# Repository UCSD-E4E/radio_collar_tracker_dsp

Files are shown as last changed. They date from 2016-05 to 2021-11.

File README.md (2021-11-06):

radio_collar_tracker_drone
====================
Airborne Wildlife Radio Collar Tracker - UAS Component

Engineers for Exploration, UCSD Project

Installing the payload software
===============================
1.	Install the required dependencies
	1.	python3
		1.	`apt-get install python3`
	2.  boost
		1.	`apt-get install libboost-all-dev`
	3.  pythom-mako
		1.	`apt-get install python-mako`
	4.  six
		1.	`pip install six`
	5.  requests
		1.	`pip install requests`
	7.  enum
		1.	`pip install enum`
	8.  pyserial
		1.  `pip3 install pyserial`
	5.	libusb-dev
		1.	`apt-get install libusb-1.0-0-dev`
	9.	libuhd 3.11.01
		1.	`apt-get install cmake build-essential`
		2.	`git clone git://github.com/EttusResearch/uhd.git`
		3.	`cd <uhd_repo>/host`
		4.	`git checkout v3.11.0.1`
		5.	`mkdir build`
		6.	`cd build`
		7.	`cmake -DENABLE_B100=OFF -DENABLE_X300=OFF -DENABLE_N230=OFF -DENABLE_USRP1=OFF -DENABLE_USRP2=OFF -DENABLE_OCTOCLOCK=OFF -DENABLE_RFNOC=OFF -DENABLE_MPMD=OFF -DENABLE_EXAMPLES=OFF -DENABLE_MANUAL=OFF -DENABLE_TESTS=OFF ../`
		8.	`make`
		9.	`make install`
		10.	`ldconfig`
		11.	`/usr/local/lib/uhd/utils/uhd_images_downloader.py -t b2xx*`
	10.	fftw
		1.	`wget http://www.fftw.org/fftw-3.3.8.tar.gz`
		2.	`tar -xzf fftw-3.3.8.targ.gz`
		3.	`cd <fftw>`
		4.	`./bootstrap.sh && ./configure --enable-threads 
		--enable-generic-simd128 --enable-generic-simd256`
		5.	`make`
		6.	`make install`
2.	Install the software
	1.	`cd <radio_collar_tracker_drone>`
	2.	`git checkout online_proc`
	2.  `./autogen.sh`
	3.  `./configure`
	4.	`make`
	5.	`sudo make install`

tl;dr
-----
1.	`sudo apt-get update`
2.	`sudo apt-get install -y git vim htop gdb valgrind cmake build-essential python3 libboost-all-dev python-mako python3-pip libusb-1.0-0-dev autoconf pkg-config picocom python-pip zip wget tmux`
3.	`sudo pip2 install six requests`
4.	`sudo pip3 install pyserial`
5.	`git clone git://github.com/EttusResearch/uhd.git`
6.	`cd uhd/host`
7.	`git checkout v3.11.0.1`
8.	`mkdir build`
9.	`cd build`
10.	`cmake -DENABLE_B100=OFF -DENABLE_X300=OFF -DENABLE_N230=OFF -DENABLE_USRP1=OFF -DENABLE_USRP2=OFF -DENABLE_OCTOCLOCK=OFF -DENABLE_RFNOC=OFF -DENABLE_MPMD=OFF -DENABLE_EXAMPLES=OFF -DENABLE_MANUAL=OFF -DENABLE_TESTS=OFF ../`
11.	`make -j8`
12.	`sudo make install`
13.	`sudo ldconfig`
14.	`sudo /usr/local/lib/uhd/utils/uhd_images_downloader.py -t b2xx*`
15.	`cd ../../..`
16.	`wget http://www.fftw.org/fftw-3.3.8.tar.gz`
17.	`tar -xzf fftw-3.3.8.tar.gz`
18.	`cd fftw-3.3.8`
19.	`./bootstrap.sh`
20.	`./configure --enable-threads --enable-generic-simd128 --enable-generic-simd256`
21.	`make -j8`
22.	`sudo make install`
23.	`cd ../`
24.	`git clone git://github.com/UCSD-E4E/radio_collar_tracker_dsp.git`
25.	`cd radio_collar_tracker_dsp`
26.	`git checkout master`
27.	`./autogen.sh`
28.	`./configure`
29.	`make -j8`
30.	`sudo make install`

Running the payload software (standalone)
=========================================
`sudo service rctrun start`

# Running the payload software (hardware-based initialization)

## Payload Power On Procedure
1.	Disconnect power to AUTOPILOT, PAYLOD
2.	Connect power to PAYLOAD
3.	Connect power to AUTOPILOT
4.	Flip PAYLOAD SWITCH to the ON position.
5.	Wait for the PAYLOAD STATUS LIGHT to turn green for at least 10 seconds.
6.	Flip PAYLOAD SWITCH to the OFF position.
7.	Wait for the PAYLOAD STATUS LIGHT to turn off within 5 seconds.
8.	Connect the GROUND CONTROL STATION to the AUTOPILOT.
9.	Payload Power On Procedure complete.

## Payload Start Procedure
1.	Complete the Payload Power On Procedure.
2.	Flip PAYLOAD SWITCH to the ON position.
3.	Wait for the PAYLOAD STATUS LIGHT to turn green for at least 10 seconds.
4.	Payload Start Procedure complete.

## Payload Stop Procedure
1.	Flip PAYLOAD SWITCH to the OFF position.
2.	Wait for the PAYLOAD STATUS LIGHT to turn off within 5 seconds.
3.	Payload Stop Procedure complete.

## Payload Power Off Procedure
1.	Complete the Payload Stop Procedure.
2.	Disconnect power to the PAYLOAD.
3.	Payload Power Off Procedure complete.

Output Data Format
==================
Output data location is specified in `/usr/local/etc/rct_config`.  Each run
consists of a number of IQ (raw) data files, GPS data files, and a metadata
file.  The name format for each type of file is `[type]_[run]_[file_num]`.  
The `type` field specifies, in capital letters, the type of file (i.e. RAW_DATA,
GPS, or META).  The `run` field specifies a numerical identifier for each run,
assigned sequentially. This field is always 6 characters wide, zero padded.  The
`file_num` field specifies the ordering of the IQ data files.  The first file
recorded would have a file number of 1, sequential files having sequential
numbers.  This field is always 6 characters wide, zero padded.

The raw data files contain the raw IQ data recorded as pairs of 8-bit unsigned
integers.  Each pair represents the in-phase and quadrature components of the
recorded signal in sequence.  See
https://en.wikipedia.org/wiki/In-phase_and_quadrature_components for an
explanation of IQ signal representation.

The GPS data files contain timestamped snapshots of autopilot telemetry.

The metadata file contains metadata pertaining to the configuration of the
payload.  Each line contains one field.  The key for each field is followed by a
colon, then the value for that field, followed by a newline character:
```
[field_name]: [field_value]
```
The whitespace between the colon and field value is optional, and preferred for
readability, but cannot be a newline.  The metadata file contains the following
fields: local IQ data start time (UTC in seconds), SDR center frequency (Hz),
SDR sampling frequency (Hz), SDR gain (dB).

# Information for Developers
## Connecting to the payload
1.	Connect to the `ubnt` GROUND WIFI LINK.
2.	Look for the sticker with the device hostname on the payload.
3.	SSH in using `e4e@hostname.local`

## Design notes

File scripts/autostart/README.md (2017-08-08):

# Operation

The autostart module should accomplish the following:
* When the switch is moved to the "on" position, execute `rct_sdr_starter`.
* Monitor the state of `rct_sdr_starter` to ensure correct operation.
* When the switch is moved to the "off" position, send `SIGTERM` to `rct_sdr_starter`.
* Enable multiple runs without rebooting the system.

# Configuring autostart

If the file `/usr/local/etc/rct_autostart` exists, autostart will be enabled.

# Pinout:
5V0 -> J13-4

1V8 -> J13-10

GND -> J13-9

GPIO1 -> J13-11

GPIO2 -> J13-13

GPIO3 -> J13-15

GPIO4 -> J13-17

GPIO5 -> J13-19

SW1 -> J13-21

# Structure
`rctstart` is the Linux Standard Base init script that starts the `rctrun` service at boot.

`rctrun` is the state machine that manages initializing and starting all devices.

`rct_blink` is the LED mapping program that drives the LEDs.

## rctstart

`rctstart` is the init script that runs at boot.  At current, this only starts and stops the `rctrun` process.  It uses the `/var/lock/rctstart` lock to ensure that only one instance of `rctrun` exists.  The source for this is `rctstart.sh`

## rctrun

`rctrun` is the state machine that manages the initialization and starting of all devices and recording.  There are several state machines for each of the GPS, SDR, and output directory.  These initialize and sanity check the devices to ensure that the next run will operate properly.  `rctrun` will automatically launch and stop the necessary programs.

`rct_blink` is the program that drives the LEDs based on the state of `rctrun`.  State information is stored in `/var/local/rct.dat`.

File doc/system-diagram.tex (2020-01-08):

\documentclass[tikz, convert={outfile=\jobname.svg}]{standalone}
\usetikzlibrary{arrows, positioning, quotes, graphs, graphdrawing, fit, topaths}
\usegdlibrary{force}
\begin{document}
	\tikz [	node distance=1 cm, 
			env/.style={}, 
			block/.style={draw,rectangle},
			every edge quotes/.append style={font=\tiny, rectangle}]{
		\node (rf) [env] {Transmitter Signal (1)};
		
		\node (ant) [block, below=of rf] {Antenna (2)};
		\node (lna) [block, below=of ant] {Low Noise Amplifier (3)};
		\node (sdr) [block, below=of lna] {Software Defined Radio (4)};
		\node (ping_detect) [block, below=of sdr] {Ping Detector (5)};
		\node (sensor_fusion) [block, below=of ping_detect] {Sensor Fusion (6)};
		\node (sys_mgr) [block, left=of sensor_fusion] {System Manager (12)};
		\node (ui_board) [block, below=of sensor_fusion] {UI Board (11)};
		\node (pgps) [block, left=of ui_board] {Payload GPS (9)};
		\node (pcompass) [block, below=of ui_board] {Payload Compass (10)};
		\node (disk) [block, right=of sensor_fusion] {Disk (13)};
		\node (obc) [draw, label={[anchor=south west]north west:On-Board Computer (14)}, fit=(ping_detect) (sys_mgr) (sensor_fusion) (disk)] {};
		
		\node (dmag) [block, left=of ant] {Drone Compass (17)};
		\node (dgps) [block, left=of dmag] {Drone GPS (18)};
		\node (px4) [block, below=of dgps] {Flight Controller (19)};
		\node (esc) [block, below=of px4] {ESCs (22)};

		\node (drone)[draw, label={[anchor=south west]north west:Drone (15)}, fit=(obc) (sdr) (lna) (ant) (ui_board) (pgps) (pcompass) (dgps) (dmag) (px4)] {};
		
		\node (ping_est) [block, left=of drone] {Ping Estimator (7)};
		\node (ping_vis) [block, below=of ping_est] {Estimate Visualization (8)};
		\node (ctrl) [block, below=of ping_vis] {Payload Control (20)};
		\node (mp) [block, left=of px4] {Vehicle Control (21)};

		\draw (rf) edge[-stealth', "RF Signal"] (ant)
			  (ant) edge[-stealth', "RF Signal over Coax"] (lna)
			  (lna) edge[-stealth', "RF Signal over Coax"] (sdr)
			  (sdr) edge[-stealth', "IQ Data"] (ping_detect)
			  (ping_detect) edge[-stealth', "Detected Pings"] (sensor_fusion)
			  (ui_board) edge[-stealth', "Sensor Data"'] (sensor_fusion)
			  (sys_mgr) edge[-stealth', "System Status"'] (ui_board)
			  (pgps) edge[-stealth', "NMEA"] (ui_board)
		      (pcompass) edge[-stealth', "Pose"] (ui_board)
			  (sensor_fusion) edge[-stealth', "Pings"] (disk)
			  				  edge[-stealth', out=150, in=0, "Pings"] (ping_est)
			  (ping_est) edge[-stealth', "Estimates"] (ping_vis)
			  (px4) edge[stealth'-, "NMEA"] (dgps)
			  		edge[stealth'-, "Heading"] (dmag)
			  		edge[stealth'-stealth', "MAVLink"] (mp)
			  		edge[-stealth', "PWM"] (esc)
			  (ctrl) edge[-stealth', out=5, in=180, "Commands"] (sys_mgr)
			  		 edge[stealth'-, out=0, in=185, "System Status"'] (sys_mgr);
		\node (gcs) [block, label={[anchor=south west]north west:Ground Control Station (16)}, fit=(ping_est) (ping_vis) (mp) (ctrl)] {};
	}

\end{document}

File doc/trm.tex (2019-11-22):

\documentclass{report}
% \usepackage{draftwatermark}
\title{Radio Collar Tracker Technical Reference Manual}
\author{Nathan Hui, Project Lead\\Engineers for Exploration, UC San Diego}
\date{\today\\v0.3}
\usepackage{fullpage,bookmark,hyperref,listings,lmodern,siunitx}
\usepackage[toc,nonumberlist]{glossaries}
\makeglossaries
\hypersetup{
    colorlinks,
    citecolor=black,
    filecolor=black,
    linkcolor=black,
    urlcolor=blue
}
\renewcommand*{\chapterautorefname}{Chapter}
\lstset{
	basicstyle=\ttfamily,
	breaklines=true
}
\renewcommand*{\chapterautorefname}{Chapter}
\begin{document}
	\maketitle
	\tableofcontents
	\listoffigures
	\listoftables
	\lstlistoflistings
	\chapter{Overview}
	\chapter{Signal Processing}
		\section{Version 1}

	\chapter{Payload}
		\section{UP Core}
			\subsection{Locating the UP Core}
				The UP Core is currently configured to automatically connect to either the Sealab or UCSD-Protected networks.  It has a hostname of e4e-UPCORE-1.

				At current, the Sealab network is configured as a bridge to the UCSD network, so all devices can be accessed via hostname.dynamic.ucsd.edu.

				The UP Core can always be accessed (on UCSD campus) at e4e-upcore-1.dynamic.ucsd.edu.

				Due to this network configuration, the UP Core is accessible only via SSH public key authentication.  To add a public key, append the appropriate key to \lstinline[language=sh]{/home/e4e/.ssh/authorized_keys}.
		\section{UI Board} \label{sec:ui}
			\subsection{Flashing the UI Board} \label{ssec:flash_ui}
				The UI Board currently uses an Atmel ATmega32u4.  The best way to flash this is to use the Dragon ISP (In System Programmer) to load the program into flash.  The recommended way to interact with the Dragon ISP for Atmel microcontrollers is by using \lstinline[language=sh]{avrdude}.  See Listing \ref{lst:avrdude_usage} for details on specific command line options.

				For the UI Board, use the following options:

				\begin{itemize}
					\item \lstinline{partno}: \lstinline{m32u4}
					\item \lstinline{bitclock}: \lstinline{10}
					\item \lstinline{programmer}: \lstinline{dragon_isp}
					\item \lstinline{port}: \lstinline{usb}
					\item \lstinline{memtype}: \lstinline{flash}
				\end{itemize}
				
				For example, if we were to flash the file \lstinline{foo.hex} to the UI Board, we would use the command in Listing \ref{lst:avrdude_example}.

				\begin{lstlisting}[language=sh, caption={Example avrdude command}, label={lst:avrdude_example}]
avrdude -p m32u4 -c dragon_isp -B 10 -P usb -U flash:w:foo.hex
				\end{lstlisting}

				\begin{lstlisting}[caption={\lstinline{avrdude} usage}, label={lst:avrdude_usage}]
Usage: avrdude [options]
Options:
  -p <partno>                Required. Specify AVR device.
  -b <baudrate>              Override RS-232 baud rate.
  -B <bitclock>              Specify JTAG/STK500v2 bit clock period (us).
  -C <config-file>           Specify location of configuration file.
  -c <programmer>            Specify programmer type.
  -D                         Disable auto erase for flash memory
  -i <delay>                 ISP Clock Delay [in microseconds]
  -P <port>                  Specify connection port.
  -F                         Override invalid signature check.
  -e                         Perform a chip erase.
  -O                         Perform RC oscillator calibration (see 
                             AVR053). 
  -U <memtype>:r|w|v:<filename>[:format]
                             Memory operation specification.
                             Multiple -U options are allowed, each request
                             is performed in the order specified.
  -n                         Do not write anything to the device.
  -V                         Do not verify.
  -u                         Disable safemode, default when running from a
                             script.
  -s                         Silent safemode operation, will not ask you 
                             if fuses should be changed back.
  -t                         Enter terminal mode.
  -E <exitspec>[,<exitspec>] List programmer exit specifications.
  -x <extended_param>        Pass <extended_param> to programmer.
  -y                         Count # erase cycles in EEPROM.
  -Y <number>                Initialize erase cycle # in EEPROM.
  -v                         Verbose output. -v -v for more.
  -q                         Quell progress output. -q -q for less.
  -l logfile                 Use logfile rather than stderr for 
                             diagnostics.
  -?                         Display this usage.
				\end{lstlisting}

			\subsection{Compiling Programs for the UI Board} \label{ssec:ui_compile}
				\subsubsection{Arduino IDE} \label{sssec:ui_arduino_compile}
					To use the Arduino IDE to compile programs, load the code into the Arduino IDE.  In the IDE, set the \lstinline{Board} option to \lstinline{Arduino Leonardo}, and enable verbose output for compilation.

					Compile the code by clicking the \lstinline{Verify} button, or by selecting \lstinline{Verify/Compile} from the \lstinline{Sketch} menu.  In the output area, look for the line that invokes \lstinline{avr-objcopy} and outputs a file that hax the \lstinline{.hex} extension.  This is the file that needs to be uploaded to the UI Board using the instructions in Subsection \ref{ssec:flash_ui}.

				\subsubsection{avr-gcc} \label{sssec:ui_make_compile}
					If the Arduino IDE is not available, or not an option, we can use the AVR compilation toolchain.  This is a version of \lstinline{gcc} that compiles specifically to the AVR instruction set.

					In general, use \lstinline{avr-g++} or \lstinline{avr-gcc} to compile the individual object files as appropriate.  Then use \lstinline{avr-g++} to link all the object files and libraries into an \lstinline{.elf} (Executable and Linkable Format).  Finally, use \lstinline{avr-objcopy} to copy the text and data portions of the program into the appropriate locations in the \lstinline{.hex} file (Intel Hexcode).

					An example compilation may look like the following:

					\begin{lstlisting}[language=sh, caption={Example avr-gcc compilation}, label={lst:avr-gcc_example}]
avr-g++ -c test.cpp -o test.o
avr-g++ -o test.elf test.o
avr-objcopy -j .text -j .data -O ihex test.elf test.hex
					\end{lstlisting}

					See the \lstinline{ui_board} branch of the Radio Collar Tracker Github\footnote{\url{https://github.com/UCSD-E4E/radio_collar_tracker_drone/blob/ui_board/src/arduino/Makefile}} for a makefile containing the rules to compile, link, and format the program.
			\subsection{UI Board Functionality}\label{ssec:ui_functional}
				The UI Board shall gather data from the following sensors: GPS, compass, and user switch.  It must transmit the data and state information to the UP Core as specified in Section \ref{ssec:ui_obc_msg}.  Simultaneously, the UI Board shall also receive status messages from the UP Core as specified in Section \ref{ssec:obc_ui_msg}, and switch LEDs in the appropriate response.  See Tables \ref{tbl:led1_states}, \ref{tbl:led2_states}, \ref{tbl:led3_states}, and \ref{tbl:led4_states} for the state tables.

				\begin{table}[htp]
					\centering
					\caption{LED 1 (System) State Table}
					\label{tbl:led1_states}
					\begin{tabular}{c|c}
						System State & LED State \\ \hline
						Init & Blinking (5 Hz)\\
						Wait for Start & Off\\
						Wait for End & Blinking (1 Hz)\\
						Finish & Solid \\
						Fail & Off
					\end{tabular}
				\end{table}

				\begin{table}[htp]
					\centering
					\caption{LED 2 (Storage) State Table}
					\label{tbl:led2_states}
					\begin{tabular}{c|c}
						Storage State & LED State \\\hline
						Init & Blinking (5 Hz)\\
						Ready & Solid \\
						Fail & Off\\
						Retry & Blinking (1 Hz)
					\end{tabular}
				\end{table}			

				\begin{table}[htp]
					\centering
					\caption{LED 3 (SDR) State Table}
					\label{tbl:led3_states}
					\begin{tabular}{c|c}
						SDR State & LED State \\\hline
						Init & Blinking (5 Hz)\\
						Ready & Solid\\
						Fail & Off\\
						Retry & Blinking (1 Hz)
					\end{tabular}
				\end{table}

				\begin{table}[htp]
					\centering
					\caption{LED 4 (GPS) State Table}
					\label{tbl:led4_states}
					\begin{tabular}{c|c}
						GPS State & LED State \\\hline
						Init & Blinking (5 Hz)\\
						Ready & Solid\\
						Fail & Off\\
						Retry & Blinking (1 Hz)
					\end{tabular}
				\end{table}

				LED 5 shall be solid in and only in the following states: GPS is Ready, SDR is Ready, STR is Ready, and Sys is wait\_start.
		\section{UI Board to GPS/Compass Protocol Specification}\label{sec:ui_gps_mag_comm_spec}
			The GPS/Compass module is a DroTek Ublox GPS and Compass Module, configured with the XL patch antenna.
			\subsection{GPS}
				The GPS is a UBlox M8N.  This has a 5V TTL UART configured with 8N1 frames and 9600 baud.  Data is transmitted as a NMEA 0183 stream, with a nominal message rate of \SI{1}{\Hz}.
			\subsection{Compass}
				The compass is a Honeywell HMC5983 magnetometer\footnote{\url{https://aerocontent.honeywell.com/aero/common/documents/myaerospacecatalog-documents/Defense_Brochures-documents/HMC5983_3_Axis_Compass_IC.pdf}}.  This has an I2C bus, with an address of \lstinline{0x3C}.  Reference the datasheet for communication protocols.
		\section{UI Board to UP Core Protocol Specification}\label{sec:obc_uibrd_comm_spec}
			Data transmission shall take place as a software serial port over USB.  This connection shall go from the CN7 connector on the UP Core to the P2 connector on the UI Board.  This physical link shall comply with USB 2.0 standards.

			The virtual serial port shall be configured as 8N1 with a baud rate of 9600.

			Data shall be formatted as JSON dictionaries.

			\subsection{UP Core to UI Board}\label{ssec:obc_ui_msg}
				The UP Core shall transmit a status message at \SI{1}{\hertz} nominal frequency. This message shall be formatted as a JSON dictionary with the following keys: \lstinline{STR}, \lstinline{SDR}, \lstinline{SYS}.  See Listing \ref{lst:upcore_status_msg} for an example message.  See Table \ref{tbl:obc_status_vals} for the status values.  These keys are not guaranteed to come in any particular order.

				\begin{lstlisting}[caption={UP Core Status Message}, label={lst:upcore_status_msg}]
{"STR": 3, "SYS": 3, "SDR": 4}
				\end{lstlisting}

				\begin{table}[htp]
					\centering
					\caption{Status Message Lookup Tables}
					\label{tbl:obc_status_vals}
					\begin{tabular}{c|c|c}
						Storage State & State Name & STR value \\\hline
						Init & \lstinline!STR_INIT! & 0\\
						Ready & \lstinline!STR_READY! & 1\\
						Fail & \lstinline!STR_FAIL! & 2\\
						Retry & \lstinline!STR_RETRY! & 3
					\end{tabular}
					
					\begin{tabular}{c|c|c}
						SDR State & State Name & SDR value \\\hline
						Init & \lstinline!SDR_INIT! & 0\\
						Ready & \lstinline!SDR_READY! & 1\\
						Fail & \lstinline!SDR_FAIL! & 2\\
						Retry & \lstinline!SDR_RETRY! & 3
					\end{tabular}
					
					\begin{tabular}{c|c|c}
						GPS State & State Name & GPS value\\\hline
						Init & \lstinline!GPS_INIT! & 0\\
						Ready & \lstinline!GPS_READY! & 1\\
						Fail & \lstinline!GPS_FAIL! & 2\\
						Retry & \lstinline!GPS_RETRY! & 3
					\end{tabular}
					
					\begin{tabular}{c|c|c}
						System State & State Name & SYS value\\\hline
						Init & \lstinline!SYS_INIT! & 0\\
						Wait for Start & \lstinline!SYS_WAIT_FOR_START! & 1\\
						Wait for End & \lstinline!SYS_WAIT_FOR_END! & 2\\
						Finish & \lstinline!SYS_FINISH! & 3\\
						Fail & \lstinline!SYS_FAIL! & 4
					\end{tabular}
				\end{table}

				Each module may enter any state at any time.
			\subsection{UI Board to UP Core}\label{ssec:ui_obc_msg}
				The UI Board shall act as a data aggregator for the UP Core, collecting telemetry and state information from the GPS, compass, and user switch.  The UI Board shall then pass these data on to the UP Core as a JSON dictionary with the following keys: \lstinline{lat}, \lstinline{lon}, \lstinline{hdg}, \lstinline{tme}, \lstinline{run}, \lstinline{fix}, \lstinline{sat}.  These keys are not guaranteed to come in any particular order.  See Table \ref{tbl:ui_board_sensor_fields} for a description of the individual fields, and Listing \ref{lst:ui_board_sensor_msg} for an example message.

				\begin{lstlisting}[caption={UI Board Sensor Message}, label={lst:ui_board_sensor_msg}]
{"lat": 327054113, "hdg": 270, "lon": -1171710165, "tme": 1530025076, "run": true, "fix": 1, "sat": 14}
				\end{lstlisting}

				\begin{table}[htp]
					\centering
					\caption{Sensor Message Field Descriptions}
					\label{tbl:ui_board_sensor_fields}
					\begin{tabular}{c|c|c|c}
						Field & Key & Data Type & Description\\\hline
						GPS Latitude & \lstinline'lat' & int & GPS Latitude in WGS84 datum, formatted as lat $\times$ 1e7\\
						GPS Longitude & \lstinline'lon' & int & GPS Longitude in WGS84 datum, formatted as lon $\times$ 1e7\\
						Vehicle Heading & \lstinline'hdg' & int & Vehicle Heading in degree East of Magnetic North\\
						GPS Time & \lstinline'tme' & int & GPS Timestamp in seconds since GPS epoch (06 Jan 1980)\\
						User Switch & \lstinline'run' & bool & True if the switch is in the ON position, False otherwise\\
						GPS Fix Type & \lstinline'fix' & int & GPS Fix, Differential GPS Fix, RTK Fix\\% TODO Fix value assignments!
						GPS Satellite Count & \lstinline'sat' & int & Number of satellites used in current fix
					\end{tabular}
				\end{table}

				This sensor data shall be transmitted at a nominal rate of \SI{1}{\hertz}.
		\section{Payload Configuration}
			All configuration options are set in the file \lstinline[language=sh]{/usr/local/etc/rct_config}.  This file is owned by \lstinline[language=sh]{root}, and should have permissions set to \lstinline{644}.
			\subsection{Center Frequency}
				The center frequency for the SDR is set to CENTER\_FREQ by the line \lstinline[language=sh]{freq=CENTER_FREQ}.  This is the center frequency the SDR is recording at, in Hz.  Due to physical limitations of the SDR, set this to be at least 1 kHz away from the nearest frequency that needs to be measured.
			\subsection{Sampling Frequency}
				The sampling frequency for the SDR is set to SAMPLING\_FREQ by the line \lstinline[language=sh]{sampling_freq=SAMPLING_FREQ}.  This is the sampling frequency that the SDR is recording at, in samples per second.  Due to physical limitations of the SDR, this value can be only be set to between 200 kHz and 56 MHz in steps of 1 Hz.  Ensure that all frequencies to be recorded are within half the sampling frequency away from the center frequency.
			\subsection{RF Gain}
				The RF gain for the SDR receive chan is set to RF\_GAIN by the line \lstinline[language=sh]{gain="RF_GAIN"}.  This is the gain that is applied to the RF signal in the LNA stage in the SDR, in dB.  Due to physical limitations of the SDR, this value can only be set to between 0 dB and 76 dB, in steps of 1 dB.  Ensure that all recorded signals are not clipping with any new gain setting.  Ideally, the loudest signal should result in an amplitude no greater than 80\% of the dyanmic range of the SDR.
			\subsection{Initializing the USRP B200-mini(-i)}
				The USRP B200-mini and USRP B200-mini-i are not capable of retaining an FPGA image between boots.  This image needs to be flashed every boot.  This can be accomplished via command line.

				\begin{lstlisting}[language=sh]
sudo uhd_usrp_probe --args="type=b200" --init-only
				\end{lstlisting}

				Images can be downloaded on Linux systems via command line.  This requires at least 200 MB of disk space.

				\begin{lstlisting}[language=sh]
sudo uhd_images_downloader
				\end{lstlisting}
		\section{Payload Autostart}
			The payload is configured to automatically initialize itself on boot, and conduct sanity checks of its internal environment.  In addition, the payload provides a simple switch interface to enable the user to start and stop recording data without needing to SSH into the payload.  This system is comprised of two components - the User Control Board, and the payload autostart software.
			\subsection{User Control Board}
				The User Control Board is located at the front of the aircraft, just below the fuselage.  The User Control Board has 5 LEDs.  From left to right (when looking at the aircraft), the LEDs are Payload Status (Green), SDR Status (Yellow), Directory Status (Orange), GPS Status (Red), and Payload Ready (Blue).  On the right of the board is the Payload Control Switch.

				\subsubsection{Status LEDs}
					The Status LEDs provide status information to the user.  On boot, the payload conducts an internal check of the connected hardware to ensure proper operation.  The status of these checks are denoted by the SDR Status LED, Directory Status LED, and GPS Status LED.
					\paragraph{SDR Status LED}
						The SDR Status LED denotes the initialization and standby status of the SDR.  Upon boot, the payload checks for the presence and state of a USRP B200 series SDR.  Upon detecting the SDR, the payload loads the firmware for the SDR.  During this time, the SDR Status LED will be blinking, approximately once a second.  Upon loading the firmware for the SDR, the payload will place the SDR in standby, whereupon the SDR Status LED will become solid.  Should the payload fail to detect an SDR, or fail to upload the firmware for the SDR, the LED will turn off.
					\paragraph{Directory Status LED}
						The Directory Status LED denotes the detection and status of the output directory for data for the payload.  Upon boot, the payload checks for the presence of the micro SD card.  Unfortunately, due to hardware issues, the payload cannot detect a micro SD card that has been left in during boot, so the micro SD card must be remounted after boot.  Upon detecting the micro SD card (device will enumerate as /dev/mmcblk0), the payload uses udev rules to mount the micro SD card to /mnt/RAW\_DATA.  After this, the payload will check the mounted filesystem for free space, to ensure that there is enough space for the next run.  The minimum required space is 9 GB, which is enough for a 20 minute run.  Should the payload fail to detect the micro SD card, or fail to detect enough free space, the LED will turn off.  The payload will attempt to detect the micro SD card again in 10 seconds, trying for 60 seconds.
					\paragraph{GPS Status LED}
						The GPS Status LED denotes the detection and state of the GPS.  Upon boot, the payload searches for and connects to the GPS serial device.  The GPS device is expected to supply NMEA data at a baud rate of 9600.  The payload then waits for the GPS device to gain a lock (defined as a 3D fix with greater than 6 satellites).  Should the payload fail to find the GPS device, or fail to receive a fix message, the LED will turn off.  If the payload is communicating with the GPS device and receiving fix messages, but the fix is not yet good enough, the LED will blink.  When the payload has found the GPS device and has determined that the GPS has a good GPS fix, then the LED will stay on.
					\paragraph{Payload Status LED}
						The Payload Status LED denotes the recording state of the payload.  The LED is blinking while the payload is actively recording data, and solid while the payload is finishing writing data to the SD card.  The LED is off during standby and initialization.
					\paragraph{Payload Ready LED}
						The Payload Ready LED denotes the ready state of the payload.  It is on only when all initialization checks have completed and the payload is standing by for the start command.
				\subsubsection{Control Switch}
					The Control Switch controls the recording state of the payload.  The switch must be in the OFF position during boot.  Flipping the switch to the ON position sets the payload to the recording state.  The payload will begin recording immediately if the initialization is complete, or as soon as the initialization completes if not complete already.  Flipping the switch to the OFF position stops the payload recording, at which point the payload finishes writing all recorded data to disk.  When the data is recorded, the payload reinitializes the system, then goes into standby mode waiting for the ON position.
				\subsubsection{Payload Autostart Software}
					The payload autostart is controlled by the rctstart Linux service, and the autostart flag in \lstinline{/usr/local/etc/rct_config}.  If the line in \lstinline{/usr/local/etc/rct_config} is autostart=false, then the payload service will not start.  The service can also be stopped once started by calling sudo service rctstart stop.
	\appendix
	\printglossaries
\end{document}

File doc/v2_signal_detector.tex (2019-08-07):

\documentclass[tikz, convert={outfile=\jobname.svg}]{standalone}
\usetikzlibrary{arrows, positioning, quotes}
\usetikzlibrary{shapes.multipart}
\begin{document}
	\begin{tikzpicture}[
						block/.style={draw,rectangle},
						every label/.append style={font=\tiny},
						every edge/.append style={draw, -stealth', shorten > = 1pt, font=\footnotesize, inner sep = 2pt, auto, align=left},]
		\node (iq_data) [] {};
		\node (fft) [block,below=of iq_data] {FFT};
		\node (f_sel) [block,below=of fft] {Frequency Select};
		\node (int) [block,below=of f_sel] {RMS Integrator};
		\node (detect) [block,below=of int] {Detector};
		\node (end) [below=of detect] {};

		\path 	(iq_data) edge[->,"IQ Data"] (fft)
				(fft) edge[->,"Waterfall Plot"] (f_sel)
				(f_sel) edge[->,"Frequency Data"] (int)
				(int) edge[->,"Signal RMS"] (detect)
				(detect) edge[->, "Ping Power"] (end);
	\end{tikzpicture}

\end{document}

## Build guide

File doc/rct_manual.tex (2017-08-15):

\documentclass{report}
\usepackage{draftwatermark}
\SetWatermarkText{ }
\SetWatermarkScale{1}
\title{Radio Collar Tracker Flight Operations Manual}
\author{Eric Lo, Project Manager\\Nathan Hui, Project Lead\\Engineers for Exploration, UC San Diego}
\date{\today\\v2.0}
\usepackage{fullpage}
\usepackage{mdframed}
\usepackage{bookmark}
\usepackage{pdflscape}
\usepackage{multicol}
\usepackage{lmodern}

% Glossaries Definition
\usepackage[toc,nonumberlist]{glossaries}
\makeglossaries
\newacronym{COG}{COG}{Center Of Gravity}
\newacronym{UAS}{UAS}{Unmanned Aerial System}
\newacronym{GCS}{GCS}{Ground Control System}
\newacronym{PIC}{PIC}{Pilot In Command}
\newglossaryentry{multirotor}{
	name=multirotor,
	description={is an unmanned aircraft with multiple propellers for lift},
	plural=multirotors
}
\newglossaryentry{quadcopter}{
	name=quadcopter,
	description={is a multirotor with 4 propellers},
	plural=quadcopters
}
\newglossaryentry{LiPo}{
	name=LiPo,
	description={is a battery using a lithium polymer chemistry},
	plural=LiPos
}
\newglossaryentry{sdr_gls}{
	name={Software Defined Radio},
	description={is a radio that uses software instead of hardware to process and interpret the signal},
	plural={Software Defined Radios}
}
\newacronym[see={[Glossary:]{sdr_gls}}]{SDR}{SDR}{Software Defined Radio\glsadd{sdr_gls}}
\newacronym{RTL}{RTL}{Return To Launch}
\newacronym{AO}{AO}{Autopilot Operator}
\newacronym{VO}{VO}{Visual Observer}
\newacronym{COTS}{COTS}{Commercial Off-The-Shelf}
\newacronym{LOS}{LOS}{Line-Of-Sight}

\usepackage{hyperref}
\hypersetup{
    colorlinks,
    citecolor=black,
    filecolor=black,
    linkcolor=black,
    urlcolor=blue
}

\renewcommand*{\chapterautorefname}{Chapter}

\begin{document}
\maketitle
\tableofcontents
\chapter{Manual Objective}
	This manual is intended for the end user of the Radio Collar Tracker system.  It is written with the expectation that the end user has some experience flying \glspl{multirotor} in semi-autonomous or autonomous modes.  This manual should not be regarded as standalone training manual for flight operations, rather, it should part of hands-on training on how to operate this system safely.  This manual contains procedures on how to safely operate this system, as well as information on how to maintain and repair the system.
\chapter{System Overview}
	\section{Mission Profile}
		This system is designed to conduct aerial surveys for the purpose of tracking and localizing wildlife collars used for biological and ecological research.  We approach this problem by flying a radio across the search area, recording the signal strength for any pings from any collars we can detect.  We can then determine the location of a collar by correlating the signal strength and the locations where we detected that particular signal strength.

		\subsection{Phases of Flight}
			The overall flight can be broken up into multiple phases of flight: pre-takeoff, takeoff, climb, survey, approach, landing, and post-landing.

			The pre-takeoff phase of flight involves configuring and setting up the system for the intended survey.  This includes completing all relevant checks, flight planning, and maintenance.

			The takeoff phase of flight involves getting the system into the air in a safe and controlled manner.  This includes the initial climb to clear any obstacles in the takeoff zone.  This may be conducted manually or via automated mission command.

			The climb phase of flight involves getting the system to the survey objective area.  This may be conducted manually or via automated mission command.

			The survey phase of flight is the largest chunk of the flight time, and is usually conducted under complete autopilot control.  This is the phase of flight where the system is actively looking for collars.

			The approach phase of flight involves getting the system from survey altitude to the landing altitude.  This may be conducted manually or via automated mission command.

			The landing phase of flight involves getting the system out of the air and on the ground in a safe and controlled manner.  This includes the final descent to clear any obstacles in the landing zone.  This may be conducted manually or via automated mission command.

			The post-landing phase of flight involves securing the system, and safely shutting down all equipment.

			Many, if not all, of these phases of flight may be programmed as part of the automated mission.  This system can be automated to the point where the autopilot is responsible for takeoff, climb, survey, approach, and landing.
	\section{Aircraft}
		\subsection{Aircraft Summary}
			The airframe used in this \gls{UAS} is a 3DR Solo, which is a \gls{COTS} \gls{quadcopter}.  We have then added an independent payload that does not interface with the aircraft control system.
		\subsection{Aircraft Specifications}
			See Section 11.1 in the 3DR Solo User Manual.
		\subsection{Transmitter Layout}
			See Sections 1.3 and 5.6 in the 3DR Solo User Manual.
		\subsection{Aircraft Layout}
			See Section 1.2 in the 3DR Solo User Manual
	\section{Payload}
		\subsection{Payload Summary}
			The payload for this \gls{UAS} is a computerized radio recorder.  We have elected to use a software defined radio as our radio front end, as this allows us to rapidly reconfigure the payload for any range of frequencies.  This is connected to an Intel Joule, which handles all of the data collection, including collecting position data from the autopilot system.  Recorded data is organized into runs, which are stored on an SD card.
		\subsection{Payload Specifications}
			\begin{itemize}
				\item Computer\hfill Intel Joule
				\item Radio \hfill USRP B200-mini(-i)
				\item Weight \hfill 125 g
			\end{itemize}
	\section{Ground Control System}
		The \gls{GCS} for this \gls{UAS} consists of a laptop running a Windows OS and the open source flight management software, MissionPlanner.  This connects to the aircraft over the SoloLink WiFi network, permitting 2-way digital communications between the \gls{UAS} and the \gls{GCS}.  From the \gls{GCS}, we are able to plan, upload, and control all missions, as well as provide the pilot with flight and diagnostic information.
		
		See \autoref{chap:FMS}.
	\section{Crew Roles}
		\subsection{Pilot In Command}
			The \gls{PIC} is responsible for the safe operation of the aircraft.  He or she is responsible for takeoff, transition to survey, return, and landing, as well as for the general pacing of the mission.
		\subsection{Autopilot Operator}
			The \gls{AO} is responsible for monitoring the flight management software and survey progress.  He or she must plan and upload the mission plan to the aircraft, confirm clearance for switching to autonomous flight modes, and monitor the \gls{UAS} as it completes the mission.  The \gls{PIC} may also take on these duties so long as doing so does not jeopardize the safety of bystanders or the aircraft.
		\subsection{Visual Observer}
			The \gls{VO} is responsible for spotting the aircraft as it flies near flight operations area boundaries.  The \gls{VO} should have some form of communications link to the PIC, and should notify the PIC if the \gls{UAS} violates any area boundaries or comes near an obstacle.  Additionally, the \gls{VO} is responsible for recovering a downed \gls{UAS} to avoid disruption of any other activities in the area, and to maintain safety within the flight operations area boundaries.

			Having a \gls{VO} does not relieve the \gls{PIC} of the responsibility of maintaining \gls{LOS} to the \gls{UAS}.
\chapter{Checklists and Flight Procedures}
	The \gls{PIC} must use the below checklists and procedures when operating the system to ensure safe and proper operation of the system.  Failure to complete all items in either checklists or procedures may result in system misconfiguration or system failure.  The \gls{PIC} is responsible for the operation of the aircraft in accordance with all relevant rules and procedures, except that the \gls{PIC} may deviate from these rules where such deviation is necessary in the interests of safety.
	\section{Battery Cold Swap Procedure}
		See Section 2.3.2 in the 3DR Solo User Manual
	\section{Preflight Inspection}
		The \gls{PIC} must complete this checklist prior to each flight, to ensure that the aircraft is safe to operate and configured correctly.  This is referenced as ``Preflight Aircraft'' on the Reference Card.
		\begin{enumerate}
			\item Aircraft Docs \hrulefill Check present.
			\item Balance \hrulefill Check that \gls{COG} is centered.
			\item SOLO BATTERY POWER SWITCH \hrulefill Set to OFF position.
			\item SOLO CONTROLLER POWER SWITCH \hrulefill Set to OFF position.
			\item SOLO BATTERY LEVEL \hrulefill Check $>$ 90\%
			\item SOLO CONTROLLER BATTERY LEVEL \hrulefill Check $>$ 25\%
			\item SDR MOUNT \hrulefill Secure in place.
			\item SDR USB CONNECTOR \hrulefill Secure in place.
			\item SDR SMA CONNECTOR \hrulefill Secure in place.
			\item SDR ANTENNA \hrulefill Secure in place.
			\item GPS \hrulefill Secure in place.
			\item GPS USB CONNECTOR \hrulefill Secure in place.
			\item PAYLOAD POWER CONNECTOR \hrulefill Secure in place.
			\item PAYLOAD USB CONNECTOR A \hrulefill Secure in place.
			\item PAYLOAD USB CONNECTOR B \hrulefill Secure in place.
			\item PAYLOAD MOUNT \hrulefill Secure in place.
			\item PAYLOAD WIFI ANTENNA \hrulefill Secure in place.
			\item Propellers \hrulefill Check that propellers are tightened.
			\item Landing Gear \hrulefill Check that landing gear are securely attached.
		\end{enumerate}
	\section{Pre Power On Check}
		\begin{enumerate}
			\item Preflight Inspection Checklist \hrulefill Complete
			\item PAYLOAD SWITCH \hrulefill Set to OFF position.
		\end{enumerate}
	\section{Power On Procedure}
		This procedure is to be completed as part of the pre-takeoff phase of flight, prior to the takeoff phase of flight.  At the end of this procedure, the aircraft and payload will have been powered up and in an idle and safe state.
		\begin{enumerate}
			\item SOLO BATTERY POWER \hrulefill Hold for 5 seconds.
			\item SOLO LEDs \hrulefill Check White in front, Red in rear.
			\item PAYLOAD STATUS LIGHT \hrulefill Check
			\item SOLO CONTROLLER POWER \hrulefill Hold for 5 seconds.
			\item SOLO CONTROLLER SCREEN \hrulefill Check for ``Hold FLY to start motors'' screen.
			\item GCS WIFI \hrulefill Check connected.
			\item GCS SOFTWARE \hrulefill Start MissionPlanner.
			\item MP LINK PORT \hrulefill Set to ``UDP''.
			\item MP LINK \hrulefill Connect.
			\item MP Local Port \hrulefill Set the local UDP port to 14550.
		\end{enumerate}
	\section{Pre-Takeoff Check}
		This check is to be completed just prior to entering the takeoff phase of flight.  At the end of this check, the aircraft will be in a state that is ready to fly.  All items within this checklist must pass to proceed to the Takeoff Procedure.
		\begin{enumerate}
			\item MP HUD \hrulefill Check that all warnings are cleared.
			\item MP PreFlight \hrulefill Check that all items are green.
			\item GPS STATUS \hrulefill Check that the GPS fix is a 3D fix.
			\item GPS SATS \hrulefill Check that at least 6 GPS satellites reported.
			\item GPS LOCATION \hrulefill Check that the GPS location is stable and reasonable.
			\item AIRCRAFT ORIENTATION \hrulefill Check that the aircraft reports a horizontal orientation.
			\item AIRSPACE \hrulefill Check that the local airspace is clear.
			\item TAKEOFF CLEARANCE \hrulefill Contact local ATC for takeoff clearance.
		\end{enumerate}
	\section{Payload Start Procedure}
		This procedure is to be completed during the pre-takeoff phase of flight, prior to the takeoff phase of flight.  The Aircraft and Payload Power On Procedure must be completed prior to executing this procedure.  At the end of this procedure, the payload will have been initiated and will be actively recording data.
		\begin{enumerate}
			\item PAYLOAD SWITCH \hrulefill Set to the ON position.
			\item PAYLOAD STATUS LIGHT \hrulefill Check for blinking.
		\end{enumerate}
	\section{Takeoff Procedure}
		This procedure is to be completed during the takeoff phase of flight, prior to the climb phase of flight.  The Pre-Takeoff Check must be completed prior to executing this procedure.  At the end of this procedure, the aircraft will be in a stable hover above the takeoff zone.
		\begin{enumerate}
			\item SOLO CONTROLLER FLY \hrulefill Hold until motor start.
			\item THROTTLE \hrulefill Set to 75\%.
		\end{enumerate}
	\section{Pre-Mission Start Check}
		This check is to be completed just prior to starting any automated mission irregardless of current phase of flight.  The aircraft must be on and stable prior to conducting this check.  At the end of this check, the aircraft will be in a state that is ready to start the mission.  All items within this checklist must pass to proceed to the Mission Start Procedure.
		\begin{enumerate}
			\item Power On \hrulefill Completed
			\item MISSION \hrulefill Uploaded and verified.
			\item WINDS \hrulefill Check $<$ 10 m/s.
		\end{enumerate}
	\section{Mission Start Procedure}
		This procedure is to be completed at the beginning of the mission phase of flight.  The Pre-Mission Start Check must be completed prior to executing this procedure.  At the end of this procedure, the aircraft will start the planned mission.
		\begin{enumerate}
			\item Pre-Mission Start \hrulefill Completed.
			\item LOCAL AIRSPACE \hrulefill Check that local airspace is clear.
			\item FLIGHT MODE \hrulefill Set to AUTO.
		\end{enumerate}
	\section{Mission End Procedure}
		This procedure may be completed at the end of the mission phase of flight.  This procedure may be completed at any point to regain control of the aircraft during a mission.  At the end of this procedure, the aircraft will be under the \gls{PIC}'s control.
		\begin{enumerate}
			\item FLIGHT MODE \hrulefill Set to LOITER.
		\end{enumerate}
	\section{Pre-Landing Checks}
		This check is to be complete prior to entering the approach phase of flight.  At the end of this check, the aircraft is cleared to begin the approach to the landing zone.
		\begin{enumerate}
			\item APPROACH \hrulefill Check that the APPROACH is clear of obstacles.
			\item TRAFFIC \hrulefill Check that no air traffic will interfere.
			\item FLIGHT MODE \hrulefill Set to LOITER.
		\end{enumerate}
	\section{Approach Procedure}
		This procedure is to be executed during the approach phase of flight.  At the end of this procedure, the aircraft will be ready to begin the landing procedure.
		\begin{enumerate}
			\item THROTTLE \hrulefill Reduce as needed.
			\item Descent Rate \hrulefill $<$ 2 m/s
		\end{enumerate}
	\section{Landing Procedure}
		This procedure is to be executed during the landing phase of flight.  At the end of this procedure, the aircraft will be on the ground and safed.
		\begin{enumerate}
			\item THROTTLE \hrulefill Reduce as needed.
			\item Descent Rate \hrulefill $<$ 2 m/s.
			\item THROTTLE \hrulefill 0\% upon ground contact.
		\end{enumerate}
	\section{Payload Stop Procedure}
		This procedure is to be executed during the post-landing phase of flight.  At the end of this procedure, the payload will be in an idle state, with the completed run saved.
		\begin{enumerate}
			\item PAYLOAD SWITCH \hrulefill Set to OFF position.
			\item PAYLOAD STATUS LIGHT \hrulefill solid.
			\item PAYLOAD STATUS LIGHT \hrulefill turns off within 1 minute.
			\item PAYLOAD READY LIGHT \hrulefill turns on after the PAYLOAD STATUS LIGHT turns off.
		\end{enumerate}
\chapter{Emergency Procedures}
	\section{Battery Fire on Ground}
		Battery fires are caused by extreme physical or electrical damage to the battery pack.  Battery fires may be preceded by significant warming and/or puffing of the battery pack.
		\begin{mdframed}[linecolor=red,linewidth=4pt]
			WARNING: \gls{LiPo} fires are chemical fires, and can release dangerous chemicals.  ABC fire extinguishers are NOT effective against the primary battery fire, but may prevent the fire from spreading.  If available, use a CO2, dry chemical, or foam extinguisher to contain the primary fire.  Do not use water to extinguish the primary fire, however, water may be used to cool a battery and fight secondary fires as appropriate.
		\end{mdframed}
		\begin{enumerate}
			\item If the battery has not caught fire yet, but is extremely warm, immediately unplug it from any devices and take the battery outside.  Place it away from flammable items and in a well ventilated area. Allow the battery to sit for at least 30 minutes.  If the battery has cooled down in 30 minutes, it will likely not catch fire, however, the battery must be disposed of properly.  If the battery is still hot, allow it to remain outside until it has cooled off.
			\item If the battery catches fire while connected to a charger, disconnect the charger from the wall, and, if safe to do so, carry the entire charging setup outside, away from flammable items and place in a well ventilated area. If not safe to do so, remove flammable items from the area and fight any secondary fires.  Do not fight the battery fire itself, as it is self-oxidizing.

			Even if the primary fire is out, if the pack is warm, additional cells may catch fire due to thermal loading.  The battery pack is not safe until the entire pack is cooled to room temperature.
			\item If the battery catches fire while connected to the aircraft, if safe to do so, remove the battery from the aircraft.  If unable to remove the battery, if safe to do so, flip the aircraft so that the battery is on top of the aircraft to reduce damage to the aircraft.  Carry the batteries and any attached items outside, away from flammable items and place in a well ventilated area.  If not safe to move the batteries, remove flammable items from the area and fight any secondary fires.  Do not fight the primary battery fire itself, as it is self-oxidizing.

			Even if the primary fire is out, if the pack is warm, additional cells may catch fire due to thermal loading.  The battery pack is not safe until the entire pack is cooled to room temperature.
		\end{enumerate}
	\section{Loss of Autopilot Datalink}
		If the autopilot operator reports loss of link to the \gls{UAS} (characterized by no data packets received for about 5 seconds), then the \gls{UAS} will automatically initiate an \gls{RTL}.  This will continue even if the aircraft datalink is recovered.  To recover, set the flight mode to LOITER.
\chapter{Maintenance}
	This section contains checklists and procedures to facilitate the maintenance and repair of the \gls{UAS}.  The \gls{UAS} must pass all items within the Delivery Check before being placed into service.  Failure of any one of these checks may result in system failure.
	\section{Charging Batteries}
		See Section 2.3.1 in the 3DR Solo User Manual.
	\section{Propellers}
		\subsection{Inspection}
		Nylon propellers should be replaced if they are damaged.  Visually inspect the propeller for abnormal tears or warping.

		\subsection{Removal}
		To remove the propeller, unscrew the propeller from the motor housing.  Silver-top propellers unscrew counterclockwise; black-top propellers unscrew clockwise.  Check the unlock icons on each propeller to see the correct directions for removing.

		\subsection{Installation}
		To install the propeller, screw the propeller onto the motor housing.  Silver-top propellers tighten clockwise; black-top propellers tighten counterclockwise.  Check the lock icons on each propeller to see the correct directions for tightening.
	
	\section{Payload Antenna}
		\subsection{Inspection}
			Ensure that the antenna is not bent or warped in any way.

		\subsection{Removal}
		To remove the payload antenna, first disconnect the payload antenna from the payload by unscrewing the SMA connector on the antenna.  Next, remove the antenna by removing the velcro straps holding the antenna to the copter.

		\subsection{Installation}
		To install the payload antenna, attach the antenna to the copter's left side using the provided velcro straps.  Ensure that the antenna is nestled in the corner made by the copter's arms and landing gear.  Next, connect the SMA connectors on the antenna and the payload.
	\section{Payload Hardware}
		\subsection{Inspection}

		\subsection{Removal}
		To remove the payload, first disconnect the payload power, autopilot telemetry cable, and payload antenna from the payload.  Next, remove the two screws holding the payload to the aircraft.

		\subsection{Installation}
		To install the payload, align the payload with the existing screw holes on the aircraft so that the user interface devices face the outside of the aircraft.  Install the two screws to secure the payload to the aircraft.  Connect the payload power, autopilot telemetry cable, and payload antenna to the payload.
\chapter{Flight Management Software}
	\label{chap:FMS}
	\section{Requirements}
		\begin{itemize}
			\item Minimum Operating System: Windows 7
			\item Known Good Mission Planner Versions: 1.3.37
		\end{itemize}
	\section{Installation}
		\begin{enumerate}
			\item Download the Mission Planner Installer from http://ardupilot.com
			\item Accept the default settings.
			\item Install the additional drivers when prompted to.
			\item Click finish.
		\end{enumerate}
	\section{Flight Planning}
		\begin{figure}[ht]
			\centering
			\caption{Mission Planner Flight Plan Screen}
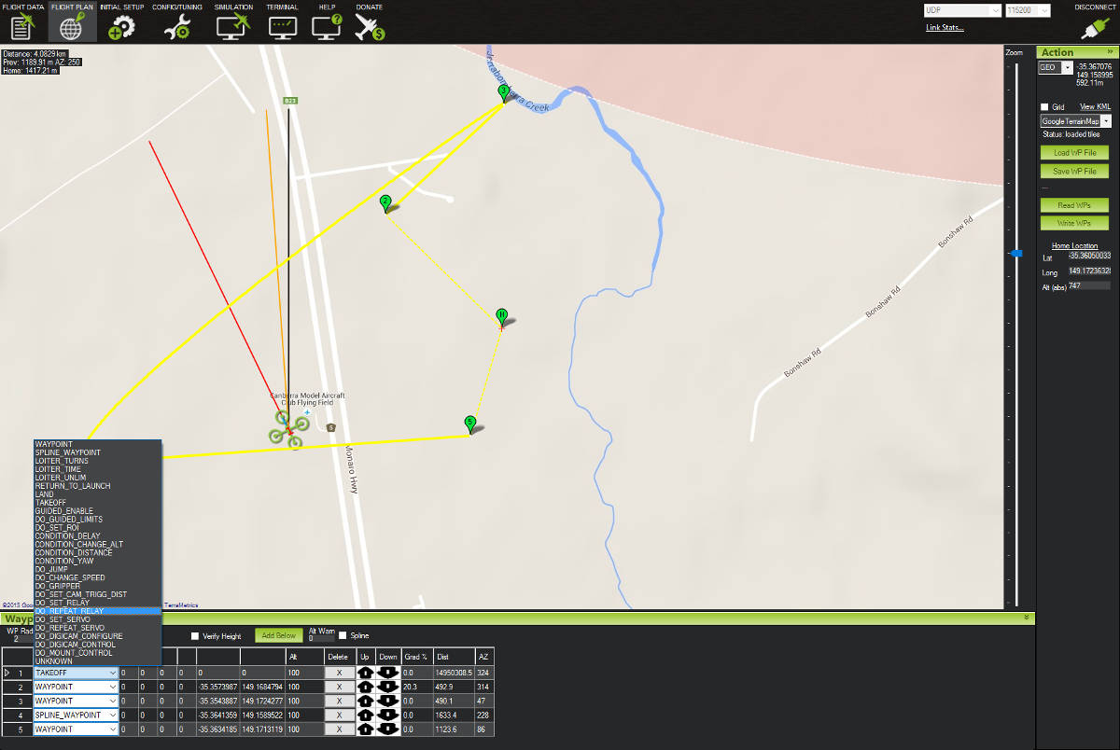
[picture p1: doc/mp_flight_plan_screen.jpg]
			
			\label{fig:mp_flight_plan}
		\end{figure}
		\subsection{Setting the Home Position}
			The HOME position represents the takeoff/landing location for the copter.  Generally, if the \gls{GCS} is connected to the \gls{UAS}, then Mission Planner can automatically update the HOME position upon \gls{UAS} arm.  However, there are occasions when this is not possible.  There are two ways to set the HOME position.

			Option 1:
			\begin{enumerate}
				\item If the new HOME location is close to the old location, simply click and drag the HOME location balloon to the desired location.  The HOME location balloon is denoted by a bold ``H'' within the balloon, or with a small label.
			\end{enumerate}

			Option 2:
			\begin{enumerate}
				\item Click and drag the map view to the desired location.
				\item Click on the ``Lat'' field.
				\item Click ``OK''.
				\item Click on the desired HOME location.
			\end{enumerate}
		\subsection{Selecting a Search Area}
			\begin{enumerate}
				\item Right click to open the context menu.
				\item Under ``Draw Polygon'', select ``Add Polygon Point''.
				\item Click ``OK''.
				\item Drag the first point to the desired location.
				\item Click to set additional points.
			\end{enumerate}
		\subsection{Loading a Search Area}
			\begin{enumerate}
				\item Right click to open the context menu.
				\item Under ``Draw Polygon'', select ``Load Polygon''.
				\item Select the polygon file you wish to load.
			\end{enumerate}
		\subsection{Saving a Search Area}
			\begin{enumerate}
				\item Right click to open the context menu.
				\item Under ``Draw Polygon'', select ``Save Polygon''.
				\item Enter the filename and directory in which you would like to save the polygon file.
				\item Click ``Save''.
			\end{enumerate}
		\subsection{Plotting a Search Grid}
			\begin{enumerate}
				\item Set a search area.
				\item Right click to open the context menu.
				\item Under ``Auto WP'', select ``Survey (Grid)''.
				\item Check the ``Advanced Options'' checkbox under ``Display'' on the right-hand sidebar.
				\item Set the desired altitude and flight speed.
				\item Check the ``Add Takeoff and Land WP's'' and ``Use \gls{RTL}'' checkboxes.
				\item Open the ``Grid Options'' tab.
				\item Set the ``Distance between lines [m]'' to 30 meters.
				\item Check that the ``Flight Time (est)'' field on the bottom bar is less than 20 minutes.
				\item Click ``Accept''.
				\item Check that the waypoints have been properly set.
			\end{enumerate}
		\subsection{Saving a Mission}
			\begin{enumerate}
				\item Click the ``Save WPs'' button in the right-hand sidebar.
				\item Select the desired directory and filename and save.
			\end{enumerate}
		\subsection{Opening a Saved Mission}
			\begin{enumerate}
				\item Click the ``Load WPs'' button in the right-hand sidebar.
				\item Navigate to the desired waypoints file and click ``Open''.
				\item Click ``OK'' when prompted to replace the HOME location.
			\end{enumerate}
	\section{Uploading a Mission}
		\begin{enumerate}
			\item Load a mission into Mission Planner.
			\item Connect to the \gls{UAS} with MAVLINK.
			\item Click the ``Write WPs'' button on the right-hand sidebar.
			\item Click the ``Read WPs'' button on the right-hand sidebar.
			\item Click ``OK'' to the dialog prompting you to reset the HOME location.
			\item Verify that the waypoints now displayed are the desired mission waypoints.
		\end{enumerate}
	\section{Operating a Mission}
		\begin{figure}[ht]
			\centering
			\caption{Mission Planner Flight Data Screen}
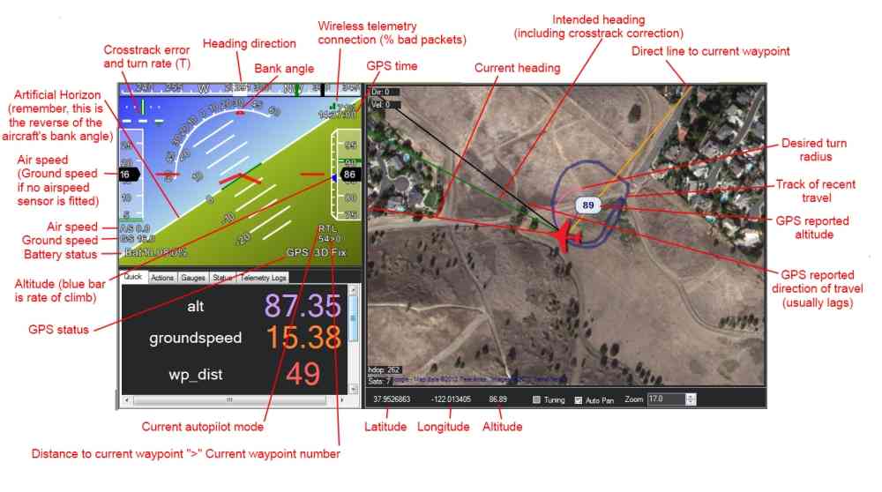
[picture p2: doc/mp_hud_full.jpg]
			
			\label{fig:mp_flt_data}
		\end{figure}
		The primary responsibility of the \gls{AO} is to monitor the \gls{UAS} as it progresses through its programmed mission using the Flight Data Screen (\autoref{fig:mp_flt_data}).  During this time, the autopilot operator should be monitoring the vital signs from the \gls{UAS}, including ground speed, mission progress, altitude, attitude, stability, battery voltage, battery consumption, power draw, and navigation stability, among other things.  In most cases, monitoring the artificial horizon and flight map will suffice - check that the \gls{UAS} is tracking properly to the waypoints, and that the aircraft has a reasonable attitude for its current speed and heading.  In addition, the \gls{AO} can use the wireless telemetry connection readout as a gauge of the quality of the autopilot datalink.  Occasionally, check the battery voltage and consumption to ensure that the \gls{UAS} has enough power to complete the mission and return.
	\section{Connecting GCS MAVLINK}
		\begin{enumerate}
			\item Select UDP.  See \autoref{fig:MP_Connect}.
				\begin{figure}[ht]
					\centering
					\caption{Connection Settings for Mission Planner}
					
					\label{fig:MP_Connect}
				\end{figure}
			\item Click the ``CONNECT'' button.
			\item Set the local port to 14550 (default).
		\end{enumerate}
\appendix
\chapter{Reference Card}
\begin{landscape}
		\begin{multicols}{3}
		\section*{Preflight Aircraft}
			\begin{tabular*}{\columnwidth}{l @{\extracolsep{\fill}} r}
				Aircraft Docs & Check\\
				Balance & Check\\
				BATT PWR SWITCH & OFF\\
				RC/TX PWR SWITCH& OFF\\
				BATT LEVEL & Check\\
				RC/TX BATT LEVEL & Check\\
				SDR MOUNT & Secure\\
				SDR USB CONN & Secure\\
				SDR SMA CONN & Secure\\
				SDR ANT & Secure\\
				GPS & Secure\\
				GPS USB CONN & Secure\\
				PAYLOAD PWR CONN & Secure\\
				PAYLOAD USB CONN A & Secure\\
				PAYLOAD USB CONN B & Secure\\
				PAYLOAD MOUNT & Secure\\
				PAYLOAD WIFI ANT & Secure\\
				Propellers & Check\\
				Landing Gear & Check\\
			\end{tabular*}
		\section*{Pre Power On}
			\begin{tabular*}{\columnwidth}{l @{\extracolsep{\fill}} r}
				Preflight Inspection & Complete\\
				PAYLOAD SW & OFF
			\end{tabular*}
		\section*{Power On}
			\begin{tabular*}{\columnwidth}{l @{\extracolsep{\fill}} r}
				BATT PWR SW & Start\\
				SOLO LEDs & Check\\
				PAYLOAD STATUS & Check TODO\\
				RC/TX PWR SW & Start\\
				RC/TX SCREEN & Check\\
				GCS WIFI & Check\\
				GCS SOFTWARE & Start\\
				MP LINK PORT & UDP\\
				MP LINK & Connect\\
				MP Local Port & 14550\\
			\end{tabular*}
		\section*{Pre Takeoff}
			\begin{tabular*}{\columnwidth}{l @{\extracolsep{\fill}} r}
				MP HUD & Check\\
				MP PreFlight & Check\\
				GPS STATUS & Check\\
				GPS SATS & Check\\
				GPS LOCATION & Check\\
				ACFT ORIENTATION & Check\\
				AIRSPACE & CLEAR\\
				TAKEOFF Clrnce & Contact\\
			\end{tabular*}
		\section*{Payload Start Procedure}
			\begin{tabular*}{\columnwidth}{l @{\extracolsep{\fill}} r}
				PAYLOAD SW & ON\\
				PAYLOAD STATUS & Check
			\end{tabular*}
		\section*{Takeoff}
			\begin{tabular*}{\columnwidth}{l @{\extracolsep{\fill}} r}
				RC/TX FLY & Start\\
				TROTTLE & 75\%
			\end{tabular*}
		\section*{Pre Mission Start}
			\begin{tabular*}{\columnwidth}{l @{\extracolsep{\fill}} r}
				Power On & Completed\\
				MISSION & Check\\
				Wind & Check
			\end{tabular*}
		\section*{Mission Start}
			\begin{tabular*}{\columnwidth}{l @{\extracolsep{\fill}} r}
				Pre Mission Start & Completed\\
				LOCAL AIRSPACE & Clear\\
				FLIGHT MODE & AUTO
			\end{tabular*}
		\section*{Mission Stop}
			\begin{tabular*}{\columnwidth}{l @{\extracolsep{\fill}} r}
				FLIGHT MODE & AUTO
			\end{tabular*}
		\section*{Pre Landing}
			\begin{tabular*}{\columnwidth}{l @{\extracolsep{\fill}} r}
				APPROACH & CLEAR\\
				TRAFFIC & CLEAR\\
				FLIGHT MODE & LOITER
			\end{tabular*}
		\section*{Approach}
			\begin{tabular*}{\columnwidth}{l @{\extracolsep{\fill}} r}
				THROTTLE & Reduce as needed\\
				Descent Rate & $<$ 2 m/s
			\end{tabular*}
		\section*{Landing}
			\begin{tabular*}{\columnwidth}{l @{\extracolsep{\fill}} r}
				THROTTLE & Reduce as needed\\
				Descent Rate & $<$ 2 m/s\\
				THROTTLE & 0\%
			\end{tabular*}
		\section*{Payload Stop}
			\begin{tabular*}{\columnwidth}{l @{\extracolsep{\fill}} r}
				PAYLOAD SW & OFF\\
				PAYLOAD STATUS & Check
			\end{tabular*}
		\end{multicols}
\end{landscape}
\printglossaries
\end{document}
\grid

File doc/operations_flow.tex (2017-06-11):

\documentclass[tikz, convert={outfile=\jobname.svg}]{standalone}
\usetikzlibrary{graphs, graphdrawing, quotes}
\usegdlibrary{layered}
\begin{document}
	\tikz [every node/.style={draw}]\graph[layered layout]{
		AOI/"Select AOI" -> plan/"Plan Flight";
		plan -> preflight/"Preflight Aircraft";
		preflight -> startrec/"Start Recording";
		startrec -> Flight;
		Flight -> stoprec/"Stop Recording";
		stoprec -> dataret/"Data Retrieval";
		dataret -> Processing;
	};
\end{document}

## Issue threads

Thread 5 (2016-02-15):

hdg datum

ntlhui, 2016-02-15:
Is the heading recorded relative to magnetic north or true north?

ntlhui, 2016-02-15:
Eric Lo: No idea on heading - would need to check source
Most likely magnetic unless you see specific correction code

ntlhui, 2016-04-26:
Should be true north - MP is configured to set declination automatically.

Closed 2016-04-26.

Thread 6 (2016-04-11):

autogen.sh output error in configure.ac

ntlhui, 2016-04-11:
automake complains:

<pre>src/sdr_record/Makefile.am:2: compiling `sdr_record.c' with per-target flags requires `AM_PROG_CC_C_O' in `configure.ac'</pre>

ntlhui, 2016-04-11:
Problem with automake.  Automake on the PI is 1.11.6.  No upgrade available via apt-get.  Automake is currently at 1.15.  Change implemented as of 1.14

ntlhui, 2016-04-12:
Fixed.

Closed 2016-04-12.

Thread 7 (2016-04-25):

Boot Sequence taking a long time

ntlhui, 2016-04-25:
^title.

ntlhui, 2016-05-03:
not sure why.  Need to instrument

ntlhui, 2016-05-10:
Check with dmesg output and HDMI output.  Possible NTP operation, or DHCP operation blocking.

ntlhui, 2016-05-11:
dmesg output:

[   48.926357] cfg80211: Calling CRDA to update world regulatory domain
[   48.966660] FAT-fs (sda1): Volume was not properly unmounted. Some data may be corrupt. Please run fsck.
[   49.437314] Adding 102396k swap on /var/swap.  Priority:-1 extents:2 across:2134012k SSFS
[   50.982044] uart-pl011 3f201000.uart: no DMA platform data
[   52.075999] cfg80211: Calling CRDA to update world regulatory domain
[   55.225950] cfg80211: Calling CRDA to update world regulatory domain
[   58.375996] cfg80211: Calling CRDA to update world regulatory domain
[   61.525958] cfg80211: Calling CRDA to update world regulatory domain
[   64.675989] cfg80211: Calling CRDA to update world regulatory domain
[   67.825956] cfg80211: Calling CRDA to update world regulatory domain
[   70.975984] cfg80211: Calling CRDA to update world regulatory domain
[   74.125958] cfg80211: Calling CRDA to update world regulatory domain
[   77.275961] cfg80211: Calling CRDA to update world regulatory domain
[   80.425966] cfg80211: Calling CRDA to update world regulatory domain
[   83.576010] cfg80211: Exceeded CRDA call max attempts. Not calling CRDA

ntlhui, 2016-05-12:
need to see dmesg before pause

ntlhui, 2016-05-12:
Removed and readded services by hand.  Cannot replicate failure.

ntlhui, 2017-04-19:
wontfix

Closed 2017-04-19.

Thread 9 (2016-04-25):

DOCS: current maintenance checks too verbose

ntlhui, 2016-04-25:
Rewrite using existing procedures.

ntlhui, 2016-05-10:
Will fix later.

Closed 2017-05-08.

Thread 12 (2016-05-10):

Limited Autopilot range

ntlhui, 2016-05-10:
Reproduce Steps:
1. Fly away

Expected result: Continued autopilot connection for at least visual range

Actual result: loss of autopilot connection within 30 meters.  No reconnection until almost identical position.

ntlhui, 2017-04-19:
critical, need to test more.  Might replace with patch antennas on controller

Closed 2017-07-07.

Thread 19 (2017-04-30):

Run number option not taking effect!

ntlhui, 2017-04-30:
run number is always 0!

ntlhui, 2017-04-30:
Possibly due to copy of run_num in pop thread?

ntlhui, 2017-04-30:
Fixed

Closed 2017-04-30.

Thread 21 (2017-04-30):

Change block transfer size

ntlhui, 2017-04-30:
http://www.tweaktown.com/image.php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

Currently using 16352 byte blocks, suggest to switch to 64k blocks

ntlhui, 2017-05-01:
Add a buffer in the push thread for 64k, change type to int16.

ntlhui, 2017-05-02:
done

Closed 2017-05-02.

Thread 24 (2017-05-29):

Broken Antenna

ntlhui, 2017-05-29:
Antenna is broken

ntlhui, 2017-05-30:
fixed

Closed 2017-05-30.

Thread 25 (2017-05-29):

Need user interface for starting and stopping

ntlhui, 2017-05-29:
145 working on this, schematic done, waiting for BOM and layout

ntlhui, 2017-07-07:
Board in fab

ntlhui, 2017-08-07:
complete

ntlhui, 2017-08-07:
See autostart

Closed 2017-08-07.

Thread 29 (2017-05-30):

Change sample rate acceptance

ntlhui, 2017-05-30:
Allow for up to 1% difference in sample rate during USRP setup.

ntlhui, 2017-06-29:
fixed

Closed 2017-06-29.

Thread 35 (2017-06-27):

GPS Format is wrong

ntlhui, 2017-06-27:
coordinates are currently ints, need to be floats, global timestamp is incorrect

ntlhui, 2017-06-28:
need to add date into timestamp for global reference

ntlhui, 2017-06-28:
corrected - needed to reconfigure GPS to output ZDA message.

Closed 2017-06-28.

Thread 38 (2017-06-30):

Occasional restart on landing?

ntlhui, 2017-06-30:
Documented today - payload had rebooted upon landing.  Possibly due to power connector?

ntlhui, 2017-08-07:
Cannot replicate

Closed 2017-08-07.

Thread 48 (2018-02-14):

GPS update internal clock

ntlhui, 2018-02-14:
Feature request

ntlhui, 2019-04-21:
won't fix, as there is now an indeterminate delay in the UI Board.

Closed 2019-04-21.

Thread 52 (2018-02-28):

Need hardware for attaching antenna

ntlhui, 2018-02-28:

ntlhui, 2018-04-05:
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

ntlhui, 2018-04-05:
Need to expand jaw by 0.1 mm.  Need to do vibration and holding testing.

ntlhui, 2019-04-28:
Increased jaw by 0.5mm, reference Rev B

ntlhui, 2019-04-29:
fit check accepted.

Closed 2019-04-29.

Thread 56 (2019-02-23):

PCB Revision

e3tran, 2019-02-23:
S2 pins are larger than hole.
P1 USB DP and DN need to be swapped to avoid cable crossover
Part for P1 is not a through-hole component
P3 is close to USB port

ntlhui, 2019-02-27:
Also need to expand keepaway around all nets

ntlhui, 2019-03-01:
Missing pullups for the I2C bus

ntlhui, 2019-03-04:
Check Radio Serial lines for swaps

ntlhui, 2019-03-04:
Reverse radio connector

ntlhui, 2019-03-04:
UP_RXD on existing is the UP Core's transmit, on ttyS0

ntlhui, 2019-03-09:
Blocking on #57

ntlhui, 2019-04-14:
Fix to #60 here

ntlhui, 2019-04-21:
Completed, sent out for fab

Closed 2019-04-26.

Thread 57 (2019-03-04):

I2C SDA Pullup Not Working

ntlhui, 2019-03-04:
I2C SDA not being pulled up, already put a 2k2 pullup on the bus near the GPS.

Unknown pull down?

ntlhui, 2019-03-09:
Test on Leonardo

ntlhui, 2019-03-15:
Simple leonardo test did not work.

ntlhui, 2019-03-15:
Reference https://www.arduino.cc/en/reference/wire, attempt to attach pullups

ntlhui, 2019-04-13:
pullups work?

ntlhui, 2019-04-13:
Prototyped on UI Board, can't bring up UI board with compass as serial device...  is the HMC5983 library clobbering the USB configuration?

ntlhui, 2019-04-13:
UI Board likely has a bad chip.  Need to rev the board to add pullups, and figure out why the UI Board sucks.

ntlhui, 2019-04-13:
UI Board ATmega32u4 SDA and SCL pins measured about 2M to ground, equivalent pins on Leonardo measure 6M to ground, no stray resistances on board after ATmega32u4 removed from UI Board.

Safe to conclude bad chip? @ericklo

Closed 2019-04-21.

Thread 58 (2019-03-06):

Arduino Dependencies for HMC5983 Library

ntlhui, 2019-03-06:
Errors for CXA Virtual functions and other Arduino dependencies, need to lock down Arduino library version.

ntlhui, 2019-03-06:
Use 1.5.5-r2 in Arduino.  Should update to arduino-avr at some point.

Closed 2019-03-06.

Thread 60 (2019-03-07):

5v supply for payload

ntlhui, 2019-03-07:
Need to power up core, ui board, and sdr

ntlhui, 2019-03-11:
Test brown out theory with bench supply

ntlhui, 2019-03-22:
https://www.digikey.com/short/p80r1t for part.  Brown out theory not confirmed nor debunked...

ntlhui, 2019-04-14:
Integrate with UI Board, merge with #56

Closed 2019-04-14.

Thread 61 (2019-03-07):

Add warning if can't find arduino library

ntlhui, 2019-03-07:
In the makefile in ui_board branch, add a check to see if the Arduino libraries are found if not, alert and make sure git submodule init was run

ntlhui, 2019-05-05:
won't fix

Closed 2019-05-05.

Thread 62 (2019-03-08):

Frequency search?

ntlhui, 2019-03-08:
Need to know the frequency to +/- 1 kHz wrt SDR...

ntlhui, 2019-03-09:
SDR has min samp_rate of 250 kHz

ntlhui, 2019-03-09:
Proposed approach:

Set SDR parameters as center_freq = tx freq, samp_rate = 250 kHz, max gain
Resample and anti-alias to 25 kHz or less, run existing classifier

Can we generate the match filter in GNUradio to prototype?

ntlhui, 2019-03-10:
Forget about resampling, proposed pipeline:

Set SDR parameters as center freq = tx freq, samp rate=250 kHz, max gain
Convert complex to magnitude
Integrate by 800
convert to dB
threshold

ntlhui, 2019-03-10:
Advise threshold using running average of 2e3 + 2 dB

Closed 2019-03-15.

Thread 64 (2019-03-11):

Add ADC logging function to UI Board

ntlhui, 2019-03-11:
Monitor 5V rail for brownout, pass back to OBC and log

ntlhui, 2019-04-14:
#56

Closed 2019-04-21.

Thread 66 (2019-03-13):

radio_collar_tracker_drone dockerfile

ntlhui, 2019-03-13:
Issues with start permissions?  Need to test.

ntlhui, 2019-04-21:
Execution with `docker run -it --rm --name rct -v /home/ntlhui/workspace/radio_collar_tracker_drone/:/root/code -v /home/ntlhui/workspace/tmp/testData/:/home/ntlhui/workspace/tmp/testData -v /media/ntlhui:/media/ntlhui --device=/dev/bus/usb/ --privileged rct`, then running `uhd_find_devices` results in `[ERROR] [USB] USB open failed: insufficient permissions.`

ntlhui, 2019-04-21:
Fixed by not using `--device` and instead mounting `/dev/bus/usb` as a volume.  Must be something to do with the way that Docker treats device trees and doesn't update them?  Updated in `run`.

Closed 2019-04-21.

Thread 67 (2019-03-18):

3DR Radio Antenna

ntlhui, 2019-03-18:
Spec tape/wire antenna to integrate onto the NW landing gear.

ntlhui, 2019-03-20:
https://www.digikey.com/short/p82j9m

ntlhui, 2020-08-24:
CU-bcn29r

ntlhui, 2021-11-11:
Closing as not relevant - 3DR Solo is obsolete platform

Closed 2021-11-11.

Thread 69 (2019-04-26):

UI Board V3 Revision

ntlhui, 2019-04-26:
USB pass-through is still swapped...
Switch is extraneous
5V line under uC might be too close to the uC pads

ntlhui, 2019-04-28:
Radio connector is still backwards!

ntlhui, 2019-04-30:
Upgrade power connectors to 22-24 AWG connectors

ntlhui, 2019-04-30:
Switch LNA to 5V

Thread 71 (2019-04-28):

Select USB Cable for SDR

ntlhui, 2019-04-28:
Needs to be appr 6 in, USB 3.0 A to USB 3.0 micro b

ntlhui, 2019-04-30:
See https://www.amazon.com/gp/product/B00T4BP91G/

Also, consider http://www.elabguy.com/datasheet/USB3u-BM-BO-V2AV%20Rev1.0.pdf

ntlhui, 2019-05-05:
Amazon part is no good, using standard cable with locked down mounts.

Closed 2019-05-05.

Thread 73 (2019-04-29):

UP Core Power Cable

ntlhui, 2019-04-29:

ntlhui, 2019-04-29:
Need a different connector - ID is wrong

ntlhui, 2019-05-01:
Done, need to fix on UI Board

Closed 2019-05-01.

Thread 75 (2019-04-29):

GPS Case Fit Check Fail

ntlhui, 2019-04-29:
Expand battery interface channel to 48.5mm wide, 0.85mm deep

ntlhui, 2019-05-03:
See Rev D

Closed 2019-05-03.

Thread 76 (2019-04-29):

Antenna Board Mount Fit Check Fail

ntlhui, 2019-04-29:
Redesign to fit ‎‎CONSMA003.062‎

ntlhui, 2019-04-29:
Also flip inserts to bottom side for better clamping pressure, and add a second set of clamping screws to the other side of the antenna

ntlhui, 2019-05-05:
won'tfix, not using antenna board anymore

Closed 2019-05-05.

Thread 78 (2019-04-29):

UI Board Boot Issue

ntlhui, 2019-04-29:
UI Board isn't booting reliably

ntlhui, 2019-05-03:
fixed, check BOOT RESET VECTOR ENABLE

Closed 2019-05-03.

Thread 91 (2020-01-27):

GCS CommandListener should be unstable

ntlhui, 2020-01-27:
Currently no checks to ignore own messages - this should be fixed.

ntlhui, 2020-08-24:
CU-bcn2fm

Closed 2024-12-17.

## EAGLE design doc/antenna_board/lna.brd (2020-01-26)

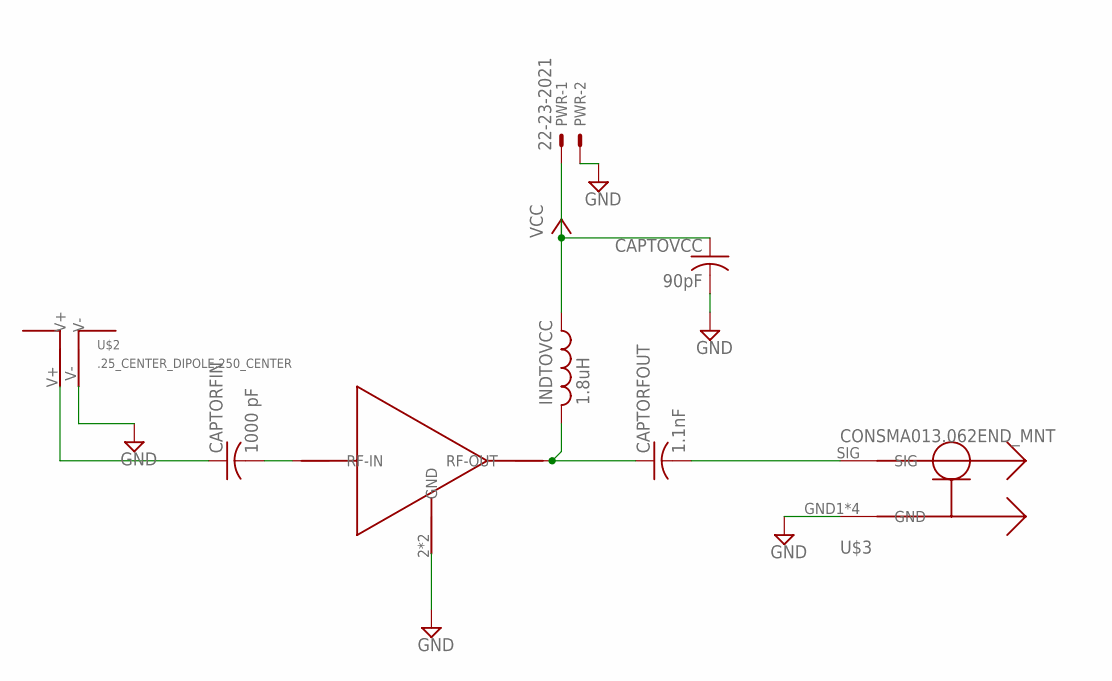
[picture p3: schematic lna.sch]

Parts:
CAPTORFIN: 1000 pF; C0603
CAPTORFOUT: 1.1nF; C0603
CAPTOVCC: 90pF; C0603
INDTOVCC: 1.8uH; L2012C
PWR: 22-23-2021
U$1: PSA4-5043+
U$2: .25_CENTER_DIPOLE.250_CENTER; .25_SPACING
U$3: CONSMA013.062END_MNT; SMA_EDGE_MNT

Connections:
GND: CAPTOVCC.2, PWR.2, U$1.2 (GND), U$1.4 (GND), U$2.V-, U$3.GND1 (GND), U$3.GND2 (GND), U$3.GND3 (GND), U$3.GND4 (GND)
unnamed: CAPTORFIN.1, U$2.V+
unnamed: CAPTORFOUT.1, INDTOVCC.2, U$1.1 (RF-OUT)
unnamed: CAPTORFOUT.2, U$3.SIG
unnamed: CAPTORFIN.2, U$1.3 (RF-IN)
VCC: CAPTOVCC.1, INDTOVCC.1, PWR.1

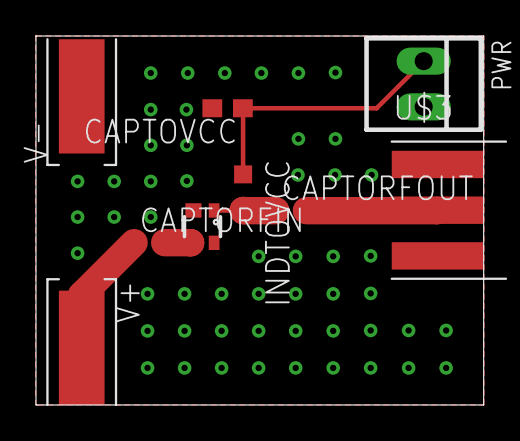
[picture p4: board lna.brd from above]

Board: 2 copper layers, 24.9 x 20.5 mm, 8 parts (0 on the bottom side), 6 nets.

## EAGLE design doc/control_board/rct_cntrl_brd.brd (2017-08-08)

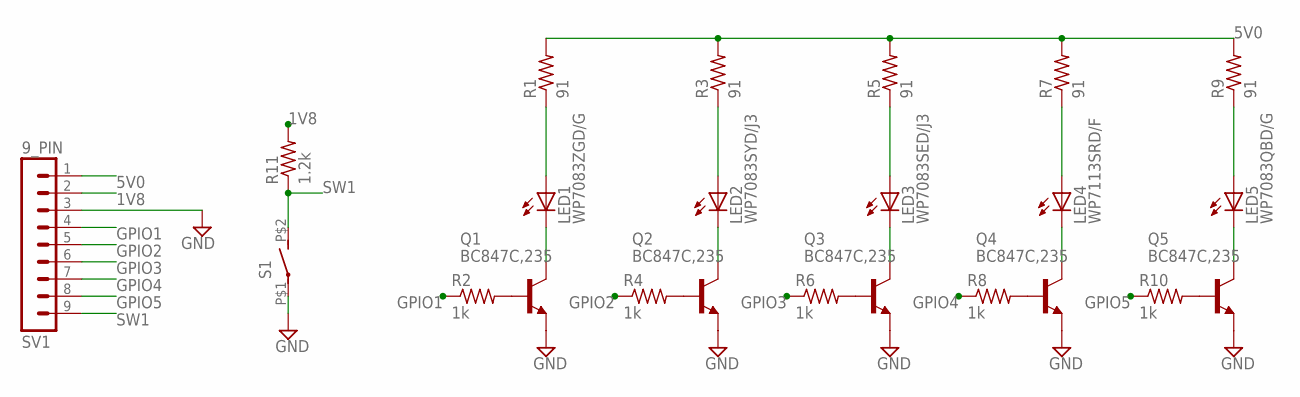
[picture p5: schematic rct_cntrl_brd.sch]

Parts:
LED1: WP7083ZGD/G; LED5MM
LED2: WP7083SYD/J3; LED5MM
LED3: WP7083SED/J3; LED5MM
LED4: WP7113SRD/F; LED5MM
LED5: WP7083QBD/G; LED5MM
Q1, Q2, Q3, Q4, Q5: BC847C,235; SOT23-BEC
R1, R3, R5, R7, R9: 91; R0603
R2, R4, R6, R8, R10: 1k; R0603
R11: 1.2k; R0603
S1: TMS6T5B2M2RE; PC_THRU_HOLE_2
SV1: 9_PIN; MA09-1

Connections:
1V8: R11.2, SV1.2
5V0: R1.2, R3.2, R5.2, R7.2, R9.2, SV1.1
GND: Q1.E, Q2.E, Q3.E, Q4.E, Q5.E, S1.P$1, SV1.3
GPIO1: R2.1, SV1.4
GPIO2: R4.1, SV1.5
GPIO3: R6.1, SV1.6
GPIO4: R8.1, SV1.7
GPIO5: R10.1, SV1.8
unnamed: LED3.K (C), Q3.C
unnamed: LED1.A, R1.1
unnamed: LED1.K (C), Q1.C
unnamed: Q1.B, R2.2
unnamed: LED2.A, R3.1
unnamed: LED2.K (C), Q2.C
unnamed: Q2.B, R4.2
unnamed: LED3.A, R5.1
unnamed: Q3.B, R6.2
unnamed: LED4.A, R7.1
unnamed: LED4.K (C), Q4.C
unnamed: Q4.B, R8.2
unnamed: LED5.A, R9.1
unnamed: LED5.K (C), Q5.C
unnamed: Q5.B, R10.2
SW1: R11.1, S1.P$2 (S), SV1.9

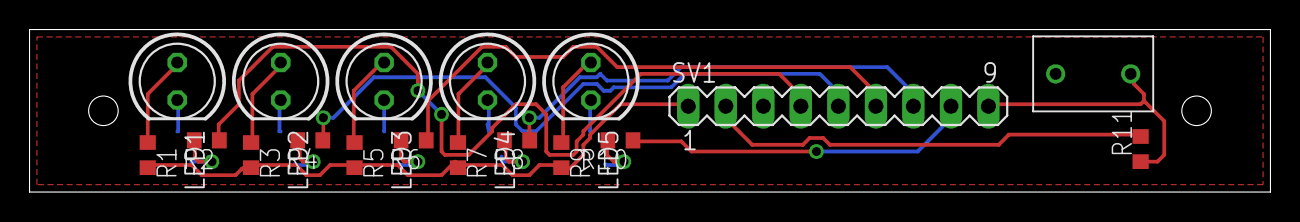
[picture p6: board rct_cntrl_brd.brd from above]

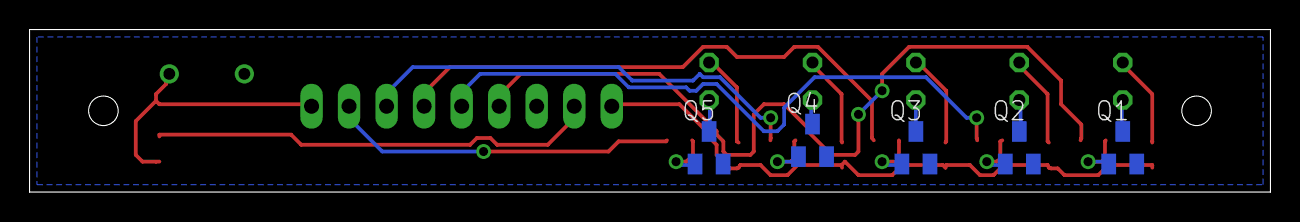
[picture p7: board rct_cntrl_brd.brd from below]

Board: 2 copper layers, 84.0 x 11.0 mm, 23 parts (5 on the bottom side), 24 nets.

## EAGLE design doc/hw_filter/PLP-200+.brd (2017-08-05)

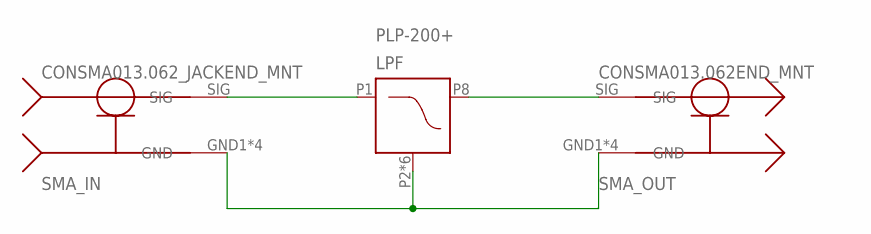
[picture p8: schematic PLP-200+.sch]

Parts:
LPF: PLP-200+; A01
SMA_IN: CONSMA013.062_JACKEND_MNT; SMA_EDGE_MNT
SMA_OUT: CONSMA013.062END_MNT; SMA_EDGE_MNT

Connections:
GND: LPF.P2 (GND), LPF.P3 (GND), LPF.P4 (GND), LPF.P5 (GND), LPF.P6 (GND), LPF.P7 (GND), SMA_IN.GND1 (GND), SMA_IN.GND2 (GND), SMA_IN.GND3 (GND), SMA_IN.GND4 (GND), SMA_OUT.GND1 (GND), SMA_OUT.GND2 (GND), SMA_OUT.GND3 (GND), SMA_OUT.GND4 (GND)
unnamed: LPF.P1 (RF_IN), SMA_IN.SIG
unnamed: LPF.P8 (RF_OUT), SMA_OUT.SIG

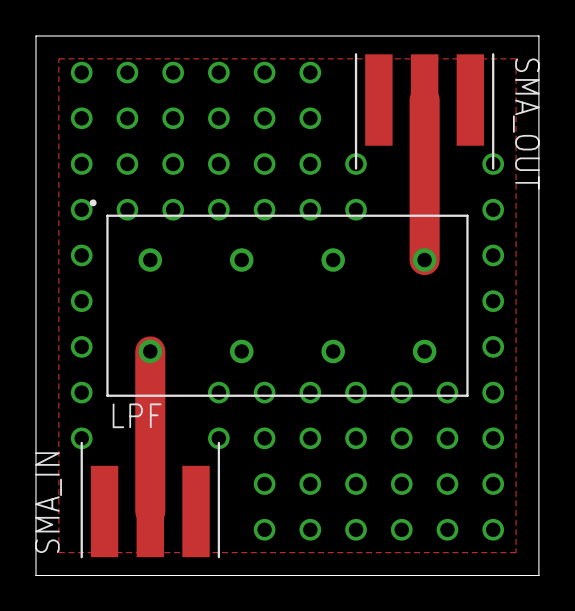
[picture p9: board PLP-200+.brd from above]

Board: 2 copper layers, 27.9 x 30.0 mm, 3 parts (0 on the bottom side), 3 nets.

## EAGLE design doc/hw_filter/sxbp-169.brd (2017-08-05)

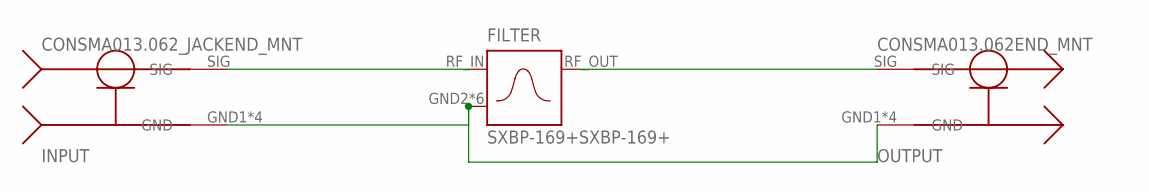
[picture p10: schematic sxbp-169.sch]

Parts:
FILTER: SXBP-169+SXBP-169+; HF1139
INPUT: CONSMA013.062_JACKEND_MNT; SMA_EDGE_MNT
OUTPUT: CONSMA013.062END_MNT; SMA_EDGE_MNT

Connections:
GND: FILTER.GND2 (GND_IN), FILTER.GND3 (GND_IN), FILTER.GND4 (GND_IN), FILTER.GND5 (GND_IN), FILTER.GND6 (GND_IN), FILTER.GND7 (GND_IN), INPUT.GND1 (GND), INPUT.GND2 (GND), INPUT.GND3 (GND), INPUT.GND4 (GND), OUTPUT.GND1 (GND), OUTPUT.GND2 (GND), OUTPUT.GND3 (GND), OUTPUT.GND4 (GND)
unnamed: FILTER.RF_IN, INPUT.SIG
unnamed: FILTER.RF_OUT, OUTPUT.SIG

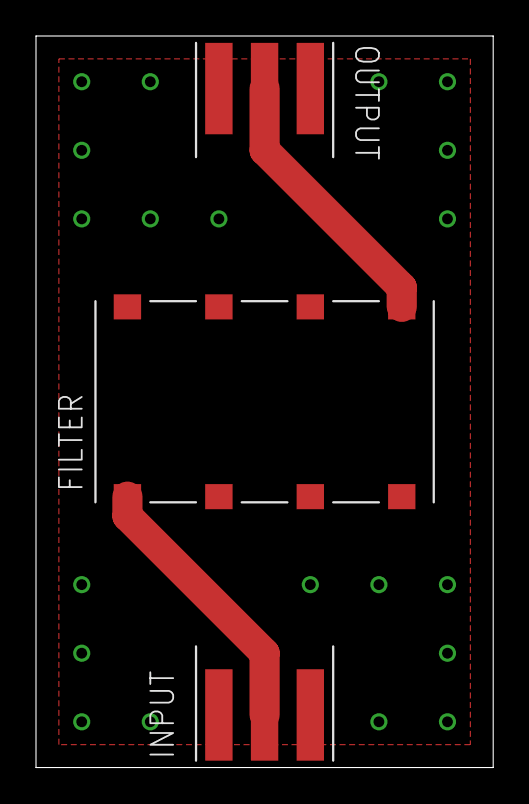
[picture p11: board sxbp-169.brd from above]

Board: 2 copper layers, 25.4 x 40.6 mm, 3 parts (0 on the bottom side), 3 nets.

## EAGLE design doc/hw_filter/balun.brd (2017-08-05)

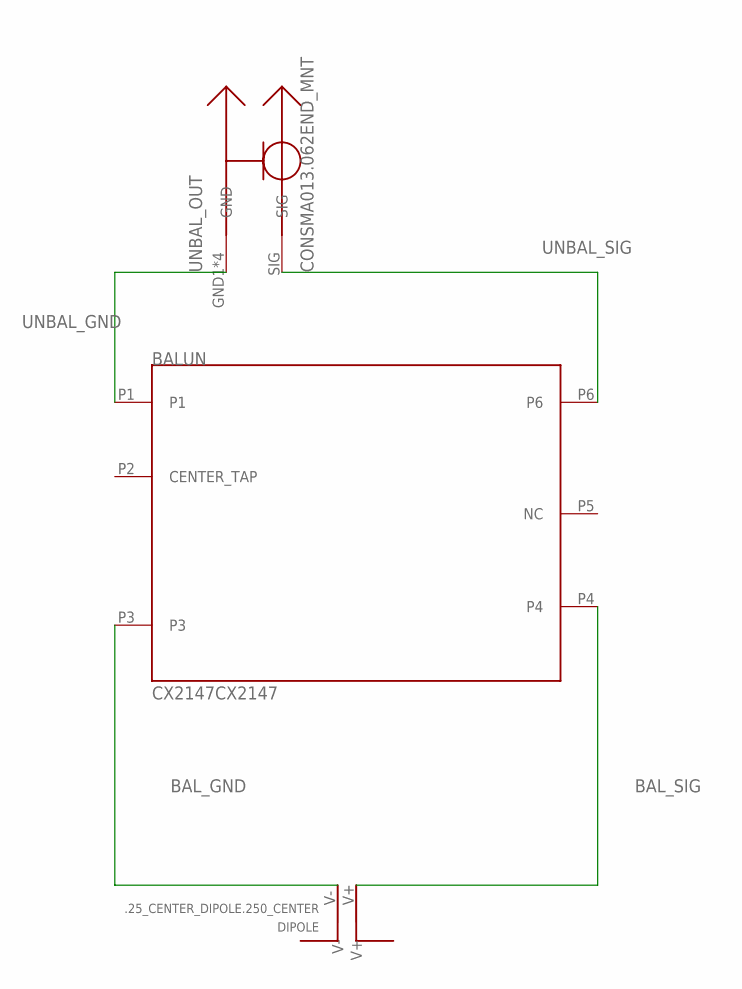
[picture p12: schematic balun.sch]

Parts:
BALUN: CX2147CX2147; 6-SMD
DIPOLE: .25_CENTER_DIPOLE.250_CENTER; .25_SPACING
UNBAL_OUT: CONSMA013.062END_MNT; SMA_EDGE_MNT

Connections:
BAL_GND: BALUN.P3, DIPOLE.V-
BAL_SIG: BALUN.P4, DIPOLE.V+
UNBAL_GND: BALUN.P1, UNBAL_OUT.GND1 (GND), UNBAL_OUT.GND2 (GND), UNBAL_OUT.GND3 (GND), UNBAL_OUT.GND4 (GND)
UNBAL_SIG: BALUN.P6, UNBAL_OUT.SIG

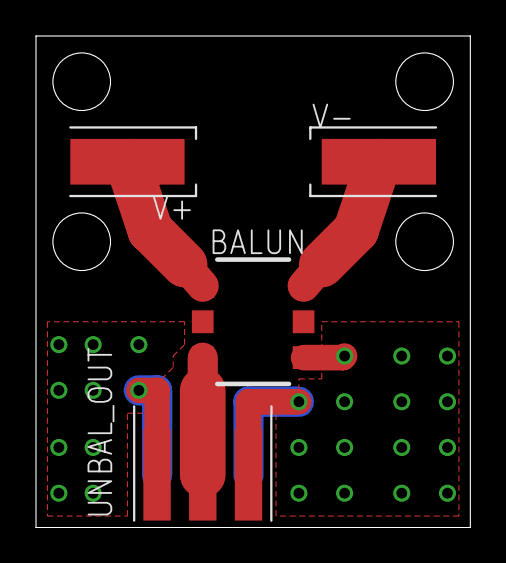
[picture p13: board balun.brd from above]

Board: 2 copper layers, 24.1 x 27.3 mm, 3 parts (0 on the bottom side), 4 nets.

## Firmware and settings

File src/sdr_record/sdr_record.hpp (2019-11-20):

#ifndef __SDR_RECORD_H__
#define __SDR_RECORD_H__

#include <complex>
#include <mutex>
#include <queue>
#include <vector>
#ifdef TEST_SDR
#include "sdr_test.hpp"
#else
#include "sdr.hpp"
#endif
#include "dsp.hpp"
#include "gps.hpp"
#include <condition_variable>
#include "localization.hpp"
#include <boost/program_options.hpp>

namespace RTT{
	/**
	 * Initial entry class.  This class is responsible for configuring and
	 * owning the component classes.
	 *
	 * This program will record and analyze RF signals from a software defined
	 * radio for pings.  These pings will be written out to a specified location.
	 */
	class SDR_RECORD final{
		/**
		 * Constructor.  This configures the signal handler and system logger.
		 */
		SDR_RECORD();

		/**
		 * Destructor.  This will close out any output streams and deinitialize
		 * allocated resources.
		 */
		~SDR_RECORD();

		/**
		 * Prints metadata about this configuration to the output directory's
		 * meta file.  This will always go in [output_dir]/META_[run_num].
		 * This information shall include start time in seconds since Unix
		 * epoch, center frequency in Hz, sampling frequency in Hz, LNA gain in 
		 * dB, data format (bytes per real sample), target frequencies, ping
		 * width in ms, ping width multipliers, GPS configuration, and test
		 * configuration.
		 */
		void print_meta_data();

		/**
		 * Parses the argument vector provided by the system as well as the
		 * configuration file.  Arguments shall adhere to the 
		 * boost::program_options conventions.
		 * @param argc Argument Count
		 * @param argv Argument Vector
		 */
		void process_args(int argc, char* const *argv);

		/**
		 * Struct to contain all configuration parameters.
		 */
		struct cmd_args{
			/**
			 * LNA gain in dB
			 */
			double gain = -1;
			/**
			 * SDR sampling rate in Hz
			 */
			std::size_t rate = 0;
			/**
			 * SDR center frequency in Hz
			 */
			std::size_t rx_freq = 0;
			/**
			 * Run identifier.  This must be unique!
			 */
			std::size_t run_num = 0;
			/**
			 * Output directory.  Output files will be stored directly in this
			 * path (i.e. data_dir/META_[run_num])
			 */
			std::string data_dir = "";
			/**
			 * Test configuration flag.  If set, this will configure the system
			 * to run as a SIL testbench.
			 * \todo documentation
			 */
			bool test_config = false;
			/**
			 * Path to pre-recorded data when used as a SIL testbench.  This
			 * must be generated with the same version of sdr_record, or the
			 * metadata may not be parsed correctly!
			 */
			std::string test_data = "";
			/**
			 * GPS target path.  For the serial GPS module, specify the Unix
			 * device handle.  For the TEST_GPS module, specify the datafile
			 * to use as a datasource.
			 */
			std::string gps_target = "";
			/**
			 * GPS baud rate.  Only used with the serial GPS module.
			 */
			std::size_t gps_baud = 9600;
			/**
			 * Nominal ping width in ms.
			 */
			std::size_t ping_width_ms = 36;
			/**
			 * Minimum ping SNR in dB above noise floor.
			 */
			double ping_min_snr = 4;
			/**
			 * Upper threshold multiplier for ping width
			 */
			double ping_max_len_mult = 1.5;
			/**
			 * Lower threshold multiplier for ping width
			 */
			double ping_min_len_mult = 0.75;
			/**
			 * Test GPS mode - this forces the TEST_NULL gps module if the
			 * test_config flag is not set.
			 */
			bool gps_mode = false;
			/**
			 * Target frequencies in Hz
			 */
			std::vector<int> frequencies;
		} args;

		/**
		 * Singleton instance pointer
		 */
		static SDR_RECORD* m_pInstance;

		/**
		 * Internal state variable
		 */
		volatile bool program_on = true;

		/**
		 * SDR data queue.  This connects the RTT::SDR and RTT::DSP_V3 classes.
		 */
		std::queue<std::complex<double>*> sdr_queue;
		/**
		 * RTT::SDR_RECORD::sdr_queue mutex
		 */
		std::mutex sdr_queue_mutex;
		/**
		 * sRTT::SDR_RECORD::dr_queue condition variable
		 */
		std::condition_variable sdr_var;

		/**
		 * Ping queue.  This connects the RTT::DSP_V3 and RTT::PingLocalizer 
		 * classes.
		 */
		std::queue<PingPtr> ping_queue;
		/**
		 * RTT::SDR_RECORD::ping_queue mutex
		 */
		std::mutex ping_queue_mutex;
		/**
		 * RTT::SDR_RECORD::ping_queue condition variable
		 */
		std::condition_variable ping_var;

		/**
		 * Software Defined Radio handle
		 */
		RTT::AbstractSDR* sdr;
		/**
		 * Digital Signal Processing stage
		 */
		RTT::DSP* dsp;
		/**
		 * Ping Localizer stage
		 */
		RTT::PingLocalizer* localizer;
		/**
		 * GPS Module
		 */
		RTT::GPS* gps;

		/**
		 * Synchronization and wake variable - this signals the main run loop
		 * when to start shutting down the component modules.
		 */
		std::condition_variable run_var;
		/**
		 * Synchronization and wake mutex for run loop
		 */
		std::mutex run_mutex;

		/**
		 * Output stream location - this is where PingLocalizer will output to.
		 */
		std::ofstream* _estimate_str;

		/**
		 * Variables map for program options.
		 */
		boost::program_options::variables_map vm;
	public:
		/**
		 * Signal handler for SIGINT. Responsible for notifying the program
		 * to begin terminating.
		 * @param sig Signal ID
		 */
		static void sig_handler(int sig);

		/**
		 * Singleton instance.
		 * @return Singleton instance of SDR_RECORD
		 */
		static SDR_RECORD* instance();
		/**
		 * Initializes this singleton with the provided command line arguments.
		 * @param argc Argument count
		 * @param argv Argument vector
		 */
		void init(int argc, char * const *argv);
		/**
		 * Start the processing.  This will not exit until all threads have
		 * completed, which will only happen after SIGINT is raised.
		 */
		void run();
	};
}

#endif

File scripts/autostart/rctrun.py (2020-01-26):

#!/usr/bin/env python3
import subprocess
import time
from enum import Enum
import threading
import os
import signal
import serial
import json
import mmap
import sys
from rct_udp_command import CommandListener
import sys
import shlex
import argparse
import datetime
import sys
import glob

WAIT_COUNT = 60

init_thread_op = True
run = True
mmap_file = None
shared_states = None
devnull = None
cmdListener = None
output_dir = None

class SDR_INIT_STATES(Enum):
	find_devices = 0
	wait_recycle = 1
	usrp_probe = 2
	rdy = 3
	fail = 4

class GPS_STATES(Enum):
	get_tty = 0
	get_msg = 1
	wait_recycle = 2
	rdy = 3
	fail = 4

class OUTPUT_DIR_STATES(Enum):
	get_output_dir = 0
	check_output_dir = 1
	check_space = 2
	wait_recycle = 3
	rdy = 4
	fail = 5

class RCT_STATES(Enum):
	init		=	0
	wait_init	=	1
	wait_start	=	2
	start		=	3
	wait_end	=	4
	finish		=	5
	fail		=	6

def get_var(var):
	var_file = open('&INSTALL_PREFIX/etc/rct_config')
	for line in var_file:
		if line.split('=')[0].strip() == var:
			value = line.split('=')[1]
			return value.strip().strip('"').strip("'")
	return None

def init_SDR(test = False):
	global init_thread_op
	global shared_states
	init_sdr_state = SDR_INIT_STATES.find_devices
	while init_thread_op:
		shared_states[0] = init_sdr_state.value
		if init_sdr_state == SDR_INIT_STATES.find_devices:
			if not test:
				uhd_find_dev_retval = subprocess.call(['/usr/local/bin/uhd_find_devices', '--args=\"type=b200\"'], stdout=devnull, stderr=devnull)
				if uhd_find_dev_retval == 0:
					init_sdr_state = SDR_INIT_STATES.usrp_probe
				else:
					init_sdr_state = SDR_INIT_STATES.fail
			else:
				time.sleep(1)
				init_sdr_state = SDR_INIT_STATES.usrp_probe
		elif init_sdr_state == SDR_INIT_STATES.wait_recycle:
			time.sleep(1)
			init_sdr_state = SDR_INIT_STATES.find_devices
		elif init_sdr_state == SDR_INIT_STATES.usrp_probe:
			if not test:
				uhd_usrp_probe_retval = subprocess.call(['/usr/local/bin/uhd_usrp_probe', '--args=\"type=b200\"', '--init-only'], stdout=devnull, stderr=devnull)
				if uhd_usrp_probe_retval == 0:
					init_sdr_state = SDR_INIT_STATES.rdy
				else:
					init_sdr_state = SDR_INIT_STATES.fail
			else:
				time.sleep(1)
				init_sdr_state = SDR_INIT_STATES.rdy
		elif init_sdr_state == SDR_INIT_STATES.fail:
			time.sleep(10)
			init_sdr_state = SDR_INIT_STATES.find_devices
		else:
			time.sleep(1)
	return 0

def init_output_dir(test = False):
	global init_thread_op
	global shared_states
	global output_dir
	init_output_dir_state = OUTPUT_DIR_STATES.get_output_dir
	counter = 0
	while init_thread_op:
		shared_states[1] = init_output_dir_state.value
		if init_output_dir_state == OUTPUT_DIR_STATES.get_output_dir:
			output_dir = get_var('output_dir')
			if output_dir is None:
				init_output_dir_state = OUTPUT_DIR_STATES.fail
			else:
				init_output_dir_state = OUTPUT_DIR_STATES.check_output_dir
			if test:
				output_dir = '/tmp/'
				if not os.path.isfile('/tmp/LAST_RUN.TXT'):
					with open('/tmp/LAST_RUN.TXT', 'w') as lastrun:
						lastrun.write('1')
		elif init_output_dir_state == OUTPUT_DIR_STATES.check_output_dir:
			if os.path.isdir(output_dir) and os.path.isfile(os.path.join(output_dir, 'LAST_RUN.TXT')):
				init_output_dir_state = OUTPUT_DIR_STATES.check_space
			else:
				init_output_dir_state = OUTPUT_DIR_STATES.wait_recycle
		elif init_output_dir_state == OUTPUT_DIR_STATES.check_space:
			if not test:
				df = subprocess.Popen(['df', '-B1', output_dir], stdout=subprocess.PIPE)
				output = df.communicate()[0].decode('utf-8')
				device, size, used, available, percent, mountpoint = output.split('\n')[1].split()
				if int(available) > 20 * 60 * 1500000 * 4:
					# enough space
					init_output_dir_state = OUTPUT_DIR_STATES.rdy
				else:
					init_output_dir_state = OUTPUT_DIR_STATES.wait_recycle
			else:
				init_output_dir_state = OUTPUT_DIR_STATES.rdy
		elif init_output_dir_state == OUTPUT_DIR_STATES.wait_recycle:
			time.sleep(1)
			counter = counter + 1
			if counter > WAIT_COUNT:
				init_output_dir_state = OUTPUT_DIR_STATES.fail
			else:
				init_output_dir_state = OUTPUT_DIR_STATES.check_output_dir
		elif init_output_dir_state == OUTPUT_DIR_STATES.fail:
			time.sleep(10)
			init_output_dir_state = OUTPUT_DIR_STATES.get_output_dir
		else:
			time.sleep(1)
	return 0

def accept_gps(msg):
	if msg.gps_qual == 0:
		return False
	if msg.gps_qual == 7:
		return False
	if msg.gps_qual == 8:
		return False
	if msg.num_sats < 6:
		return False
	return True

def init_gps(test=False):
	global init_thread_op
	global run
	global shared_states
	init_gps_state = GPS_STATES.get_tty
	counter = 0
	msg_counter = 0
	tty_stream = None

	prev_gps = 0

	while init_thread_op:
		shared_states[2] = init_gps_state.value
		if init_gps_state == GPS_STATES.get_tty:
			tty_device = get_var('gps_target')
			tty_baud = get_var('gps_baud')
			if not test:
				try:
					tty_stream = serial.Serial(tty_device, tty_baud, timeout = 1)
				except serial.SerialException as e:
					init_gps_state = GPS_STATES.fail
					print("GPS fail: bad serial!")
					print(e)
					continue
				if tty_stream is None:
					init_gps_state = GPS_STATES.fail
					print("GPS fail: no serial!")
					continue
				else:
					init_gps_state = GPS_STATES.get_msg
			else:
				init_gps_state = GPS_STATES.get_msg

		elif init_gps_state == GPS_STATES.get_msg:
			if not test:
				try:
					line = tty_stream.readline().decode("utf-8")
				except serial.serialutil.SerialException as e:
					init_gps_state = GPS_STATES.fail
					print("GPS fail: no serial!")
					continue
				if line is not None and line != "":
					msg = None
					try:
						msg = json.loads(line)
						init_gps_state = GPS_STATES.rdy
					except json.JSONDecodeError as e:
						init_gps_state = GPS_STATES.fail
						print("GPS fail: bad message!")
						init_gps_state = GPS_STATES.get_msg
						continue
				else:
					init_gps_state = GPS_STATES.get_msg
			else:
				time.sleep(1)
				init_gps_state = GPS_STATES.rdy
		elif init_gps_state == GPS_STATES.wait_recycle:
			time.sleep(1)
			if counter > WAIT_COUNT / 2:
				init_gps_state = GPS_STATES.fail
				print("GPS fail: bad state!")
				continue
			else:
				init_gps_state = GPS_STATES.get_msg
		elif init_gps_state == GPS_STATES.fail:
			time.sleep(10)
			init_gps_state = GPS_STATES.get_tty
		else: # init_gps_state = GPS_STATES.rdy
			if not test:
				try:
					line = tty_stream.readline().decode("utf-8")
				except serial.serialutil.SerialException as e:
					init_gps_state = GPS_STATES.fail
					print("GPS fail: no serial!")
					continue
				if line is not None and line != "":
					msg = None
					try:
						msg = json.loads(line)
					except json.JSONDecodeError as e:
						init_gps_state = GPS_STATES.fail
						print("GPS fail: bad message!")
						print(e)
						init_gps_state = GPS_STATES.get_msg
						continue
			else:
				time.sleep(1)
			current_gps = datetime.datetime.now()
			if prev_gps == 0:
				continue
			else:
				if (current_gps - prev_gps).total_seconds() > 5:
					init_gps_state = GPS_STATES.wait_recycle
			prev_gps = current_gps
	return 0

def init_state_complete():
	global shared_states
	return SDR_INIT_STATES(shared_states[0]) == SDR_INIT_STATES.rdy and \
		OUTPUT_DIR_STATES(shared_states[1]) == OUTPUT_DIR_STATES.rdy and \
		GPS_STATES(shared_states[2]) == GPS_STATES.rdy

def init_RCT(test = False, test_data = ''):
	global run
	global init_thread_op
	global cmdListener
	init_RCT_state = RCT_STATES.init
	
	if test:
		assert(len(test_data) != 0)
		assert(os.path.isdir(test_data))

	while run:
		shared_states[3] = init_RCT_state.value
		if init_RCT_state == RCT_STATES.init:
			init_SDR_thread = threading.Thread(target=init_SDR, kwargs={'test':test})
			init_output_thread = threading.Thread(target=init_output_dir, kwargs={'test':test})
			init_gps_thread = threading.Thread(target=init_gps, kwargs={'test':test})
			init_SDR_thread.start()
			init_output_thread.start()
			init_gps_thread.start()
			init_RCT_state = RCT_STATES.wait_init
		elif init_RCT_state == RCT_STATES.wait_init:
			# wait for init state machines to complete
			time.sleep(1)
			init_state = init_state_complete()
			if init_state:
				init_RCT_state = RCT_STATES.wait_start
			else:
				init_RCT_state = RCT_STATES.wait_init
		elif init_RCT_state == RCT_STATES.wait_start:
			time.sleep(1)
			switch_state = shared_states[4]
			if switch_state:
				print("Got start flag!, running")
				init_RCT_state = RCT_STATES.start
				init_thread_op = False
				init_SDR_thread.join()
				init_output_thread.join()
				init_gps_thread.join()
			else:
				init_RCT_state = RCT_STATES.wait_start
		elif init_RCT_state == RCT_STATES.start:
			print("Starting drone_run")
			if not test:
				with open(os.path.join(output_dir, 'LAST_RUN.TXT')) as lastrun:
					last_run = int(lastrun.readline().strip())
				with open(os.path.join(output_dir, 'LAST_RUN.TXT'), 'w') as lastrun:
					lastrun.write(str(last_run + 1))
				run_num = last_run + 1
			else:
				meta_file = glob.glob(os.path.join(test_data, 'META_*'))
				assert(len(meta_file) == 1)
				run_num = int(os.path.basename(meta_file[0]).split('_')[1])
			run_dir = os.path.join(output_dir, 'RUN_%06d' % (run_num))
			if not test:
				os.makedirs(run_dir)
			else:
				try:
					os.makedirs(run_dir)
				except:
					pass

			localize_file = os.path.join(run_dir, 'LOCALIZE_%06d' % (run_num))
			with open(localize_file, 'w') as file:
				file.write("")
				
			cmdListener.setRun(run_dir, run_num)
			time.sleep(1)

			sampling_freq = int(get_var('sampling_freq'))
			center_freq = int(get_var('center_freq'))

			if not test:
				sdr_record_cmd = ('sdr_record -g 22.0 -s %d -c %d'
					' -r %d -o %s | tee -a /var/log/rtt.log' % (sampling_freq, center_freq, run_num, run_dir))
			else:
				sdr_record_cmd = ('sdr_record -g 22.0 '
									'-s %d ' % (sampling_freq) +
									'-c %d ' % (center_freq) +
									'-r %d ' % (run_num) +
									'-o %s ' % (run_dir) +
									'--test_config ' +
									'--test_data %s' % (test_data) +
									'| tee -a /var/log/rtt.log')

			sdr_record = subprocess.Popen(sdr_record_cmd, shell=True)
			
			init_RCT_state = RCT_STATES.wait_end
		elif init_RCT_state == RCT_STATES.wait_end:
			time.sleep(1)
			switch_state = shared_states[4]
			if switch_state:
				init_RCT_state = RCT_STATES.wait_end
			else:
				init_RCT_state = RCT_STATES.finish
				print('Got stop flag!, stopping')
			if sdr_record.poll() != None:
				init_RCT_state = RCT_STATES.fail
				print('SDR Record failed!')
		elif init_RCT_state == RCT_STATES.finish:
			sdr_record.send_signal(2)
			rct_retval = sdr_record.wait()
			if not rct_retval:
				init_RCT_state = RCT_STATES.fail
			subprocess.call(['sync'])
			init_RCT_state = RCT_STATES.init
		elif init_RCT_state == RCT_STATES.fail:
			switch_state = shared_states[4]
			if switch_state:
				init_RCT_state = RCT_STATES.fail
			else:
				init_RCT_state = RCT_STATES.init

	init_SDR_thread.join()
	init_output_thread.join()
	init_gps_thread.join()

def sigint_handler(signal, frame):
	print("Received sig")
	global init_thread_op
	global run
	init_thread_op = False
	run = False

def main():
	'''Main RCT Bootstrap function
	
	Main function
	'''
	parser = argparse.ArgumentParser(description='RCT Boostrapper')
	parser.add_argument('--autostart', action='store_true')
	parser.add_argument('--test', action='store_true')
	parser.add_argument('--test_data', action='store')

	args = parser.parse_args()

	if args.test:
		assert(len(args.test_data) > 1)

	global cmdListener
	# Check for autostart
	autostart_flag = get_var('autostart')
	if autostart_flag != 'true' and args.autostart:
		print("Autostart not set!")
		return
	# Set up mmap files
	global shared_states
	if not os.path.isdir('/var/local/rct'):
		os.makedirs('/var/local/rct')

	devnull = open('/dev/null', 'w')

	mmap_file = open('/var/local/rct/status.dat', 'w+b')
	mmap_file.write(('\0' * 5).encode('utf-8'))
	mmap_file.flush()
	shared_states = mmap.mmap(mmap_file.fileno(), 5)

	cmdListener = CommandListener(shared_states, 4)

	signal.signal(signal.SIGINT, sigint_handler)
	signal.signal(signal.SIGTERM, sigint_handler)

	init_RCT_thread = threading.Thread(target=init_RCT, kwargs={'test':args.test, 'test_data':args.test_data})
	init_RCT_thread.start()

	signal.pause()

	cmdListener.stop()

	init_RCT_thread.join()

	shared_states.close()
	mmap_file.close()

if __name__ == '__main__':
	print(sys.argv)
	main()

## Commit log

2013-12-30 resize current images
2013-12-30 replaced antenna pulse image (.bmp) with .png
2014-08-30 Summer 2014 Developments
    Radio Collar Tracking Software Components, including all the BeagleBone
    Programs and the Post Processing Programs.
    [DIST_000351.csv, DIST_000359.csv, DIST_000366.csv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]
2015-02-01 Added altitude filter program
2015-02-02 Reverted gain value generation code to handle the dB * 10 storage of dB values, added gain value print
2015-02-02 Removed binaries and test files
    [META_000367.csv, META_000368.csv, META_000369.csv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]
2015-03-06 Added Matlab heatmap scripts
2015-04-16 Modified for current collars
2015-04-24 Removed debug statement for printing center frequency
2015-06-23 Added wiring schematic
    [wiring.sch]
2015-07-28 Continued implmentation of gain and recording blocks. Need to switch to C++11 for threading library
2015-07-31 Version 1 of C++ recorder. Problem is, callback isn't working (linking to a c library). Switching back to c
2015-08-01 Changed run condition, added thread join
2015-08-01 Switched to recording float instead of byte
2015-08-03 Switched back to recording 8-bit unsigned integers
2015-08-03 Added max/min sample check
2015-08-05 Added sample_mag to clean target
2015-08-25 Added parser kill function, RAW_DATA mount script target
2015-08-25 Added command to unmount BBB data partition prior to removing mount point
2015-09-08 Switched to blocking reads
2015-11-16 Added LED export command
2015-11-16 Fixed case function
2015-11-16 Added power off message
2015-11-25 Added modular device id
2016-04-04 Removed extraneous arduino libraries
2016-04-04 Moved payload wiring diagram to docs
    [payload_ui_wiring.sch]
2016-04-04 Removed obsolete BBB code
    [DIST_000351.csv, DIST_000359.csv, DIST_000366.csv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]
2016-04-04 Removed backup BBB code and old post-processing code
    [META_000367.csv, META_000368.csv, META_000369.csv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]
2016-04-07 Added brackets to init macro, added automake init macro, checking for python and bash and sed, checking for librtlsdr, updated makefile refs
2016-04-21 Updated uninstall to remove rct_mount_RAW_DATA, updated mount_RAW_DATA to target /dev/sda1
2016-04-23 Added missio profile, aircraft summary, payload summar, GCS summary, PIC role, AO role, Payload Checks, Prop Change procedure, FMS Installation
2016-04-24 Switched MANUAL to STABILIZE, updated delivery checks to reduce range, fixed Mission Planner known good versions, Added Flight Planning section
2016-04-25 Added draft watermark, fixed flight time and range, added Tx, GCS, ACRFT layout, added parallel adapter check to preflight, added throttle down and mode switches to TX checks, added payload start pro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
2016-04-26 Added the Arm Replacement Procedure
2016-04-26 Added payload antenna replacement procedure
2016-04-28 Added weights, added battery charging procedure
2016-05-02 Added payload layout, added power wiring diagram
2016-05-02 Revert "Added payload layout, added power wiring diagram"
    tmp contains files used to generate certain doc images
    This reverts commit 6d5a725a9ddad87b25677374cd2d3cd9e8141bc2.
2016-05-02 Revert "Revert "Added payload layout, added power wiring diagram""
    Undoing wrong undo
    This reverts commit 0323f9334ad8231d8b02b0611bd116eed051851b.
2016-05-05 Fixed procedures, extracted rotor alignment, removed watermark, spell check
2016-06-21 Updated mode switch
2016-07-27 Added making the mount point
2017-04-08 Fixed print_help to always print help when asked to
2017-04-09 Fixed termination condition for the writing thread
2017-04-19 Fixed system includes, added new headers for new queue, added new constants for new writer thread behavior, added new queue, changed all vprintfs to syslog commands, some reformatting
2017-04-19 Removed led references and removed SDR log
2017-06-11 Added flowcharts
2017-06-29 Allowing for sample rate difference of 1%
2017-07-22 Added hw filters data
    [balun.brd, balun.sch, jcbp-290.brd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]
2017-07-22 Added hardware definitions
    [rct_cntrl_brd.brd, rct_cntrl_brd.sch]
2017-07-27 Added LPF filters
    [PLP-200+.brd, PLP-200+.sch]
2017-07-27 Added PLP-250+ board
    [PLP-250+.brd, PLP-250+.sch]
2017-07-29 updated libraries
    [PLP-200+.brd, PLP-200+.sch, PLP-250+.brd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]
2017-08-01 Added ready and fail states
    [rctrun.py]
2017-08-02 Enabled mraa, fixed threads
2017-08-02 Attempt to fix GPS state machine
    [rctrun.py]
2017-08-02 Fixed SDR state machine to fail automatically if not USRP not found
    [rctrun.py]
2017-08-02 Changed DIR state machine to fail automatically if FS not set up
    [rctrun.py]
2017-08-02 Removed old mount script
2017-08-03 Added modular pin assignments
2017-08-03 Added switch state machine
2017-08-03 Added GPS nonexistent fail
    [rctrun.py]
2017-08-03 Updated location of mount and unount scripts
2017-08-03 Added pin execute
2017-08-03 Fixed pin direction
2017-08-03 started thread
2017-08-03 Updated LED schema
2017-08-03 Fixed led scheme
2017-08-03 Fixed SD card state machine
    [rctrun.py]
2017-08-04 Added auto reset on fail
    [rctrun.py]
2017-08-04 Increase GGA fail count
    [rctrun.py]
2017-08-04 Flipped switch for boot compability
    [rctrun.py]
2017-08-04 Fix switch in exit
    [rctrun.py]
2017-08-15 Switched to RMC
2018-04-05 Initial LNA antenna board, initial design by Brian Wong (bmw019@ucsd.edu)
    [lna.brd, lna.sch]
2019-01-06 Switched to circular buffer
2019-02-06 Added TEST_SDR flag for switching to the test SDR
2019-02-13 Added current UI board
    [ui_board.brd, ui_board.sch]
2019-02-13 Removing old schematics
    [payload_ui_wiring.sch]
2019-02-27 Updated trm to include info about programming UI board
2019-03-06 Added Arduino 1.5.5-r2 for library reference
2019-03-07 Changed submodule from ssh to https, updated Makefile to remove cJSON and I2C library paths
2019-03-15 Switched the DSP core over to the energy detector instead of frequency detector
2019-04-06 Added LED Status Blinking
2019-04-25 Added link to host devices
2019-04-25 Added mounting for host devices
2019-05-01 Added double brackets for bash-iness
2019-05-01 modularized the debug directory mount
2019-05-02 Added I2C state bypass
2019-05-03 Fixed prints
2019-05-05 Removed extraneous prints
2019-05-05 Removed extraneous print
2019-06-30 Optimized streaming and changed DSP to single thread - WIP
2019-07-16 Fixed device arguments, added timing checks
2019-07-16 Added debug and power function
2019-07-20 Disabled frequency print, optimized GPS buffer code
2019-07-25 Removed extraneous print messages
2019-07-28 Fixed data store device name
2019-07-29 Added UDP switches
2019-07-29 switched to python3, added command GUI
2019-07-29 Added start/stop buttons
2019-07-31 added switch for manual run
2019-07-31 switching to default python
2019-07-31 switched to python3 tkinter
2019-07-31 Fixed autostart flag, status serialization
    [rctrun.py, udp_command.py]
2019-08-04 Added print
2019-08-04 Fixed options and write options
    [udp_command.py]
2019-08-04 Added socket fixes
2019-08-04 Fixed sockets
2019-08-04 Fixed sockets?
2019-08-04 Added socket retry
2019-08-04 Fixed lack of upgrade status
    [udp_command.py]
2019-08-06 Added print e for serial fail
    [rctrun.py]
2019-08-07 Fixed update and auto restart
    [udp_command.py]
2020-01-26 Forked radio_collar_tracker_uib
    [ui_board.brd, ui_board.sch]
